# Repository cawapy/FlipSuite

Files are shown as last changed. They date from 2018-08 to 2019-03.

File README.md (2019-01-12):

# FlipSuite

KiCad schematics and PCBs for building flip dot and flip segment display drivers.

## USE AT YOUR OWN RISK

The designs are not yet finalized or not fully tested.

## Status

### Flips5, Flips6, Flips7

PCBs of [Flips5](Flips5), [Flips6](Flips6) and [Flips7](Flips7),
each in Version V1.0, have been manufactured and equiped.

Flips5, Flips6 and Flips7 can be considered working, at least in single display configurations. Successfully tested:

* Flips5 with standard Brose displays on ``BROSE60`` and ``BRDIC1``, connected to Flips6 on ``CNY1``+``CNY2`` and ``CNX1``
    * 28x16 (15 mm dots)
    * 28x19 (10 mm dots)
* Flips5 with extended 28x24 (10 mm dots) Brose display on ``BROSE60``+``BROSE20`` and ``BRDIC1``, connected to Flips6 on ``CNY1``+``CNY2`` and ``CNX1``
    * This display uses the 24 rows 3-26
* Flips5 with Brose display of 5 digits a 5x7 = 25x7 on ``BROSE34`` and ``BRDIC1``, connected to Flips6 on ``CNY1`` and``CNX1``
* Flips7 with Transit Media displays, connected to Flips6 ``CNY1``+``CNY2`` and ``CNX1``
    * 28x13 (15 mm dots)
    * 28x16 (15 mm dots)
    * 14x16 (15 mm dots)
    * 28x16 (10 mm dots)

Tests of multi display configurations with Flips6 are still pending.

### Flips8

[Flips8](Flips8) is work-in-progress.

## PCBs

View PCBs [online](PCBs.md).

## Known Issues V1.0

### Flips5

* ``R1``, ``R2``, ``R3`` and ``C1``, ``C2``, ``C3`` are too close to the DIP40 sockets of ``IC1``, ``IC2``, ``IC3``;
  When using standard DIP40 sockets with rectangular spring contacts,
  the socket frame and a pad of each of the mentioned resistors and capacitors will overlap.
    * Already rearranged the resistors and capacitors in the layout ([db15812: "Place FP2800As' bypass capacitors and EN-pulldowns to fit in Dip40 socket"](https://github.com/cawapy/FlipSuite/commit/db15812063dd6a5a91f173546fd940a55fbdb63b))
    * Options for manufactured boards
        * Use sockets with slimmer frame (e.g. those with round pins); or pin rows, they are also slimmer than the standard socket frames
        * Use little solder for Rs and Cs, decenter Rs and Cs away from socket frame as much as possible
        * Mill small holes into socket to not collide with housings of Rs and Cs
        * Do not equip the Flips5 PCB with those Rs and Cs
            * The enable signals should have pull down resistors, but they can be provided externally; the Flips6 already provides the enable signals *with* pull down resistors
            * The bypass capacitor can be omitted while the circuit will still work (but it *might* create more radio interferences then)
* Cannot use connector socket *with locks* for ``CN3`` due to conflict with ``BRDIC1`` connector

### Flips6

* Legend with pinout table of ``CN1`` has labels for pins 6 and 8 (``CLK`` vs. ``LAT``) swapped
    * Solution: in the layout, already fixed the table ([aecff96: "Fix wrong labels of Flips6 uP connector: LAT \<--\> CLK"](https://github.com/cawapy/FlipSuite/commit/aecff968aa479d9d29c823dc3a2e2e32617ff91e))

### Flips7

* The jumper ``JP1`` allowing to switch between 28 and 14 column display panel is not required.
  It turned out that both display types do *not* differ regarding pins of columns 4 (and 27).
  The 14 column panel can be used like the 28 column panel.
    * The jumper can be set or even soldered for the 28 column configuration.
    * Jumper to be removed in next version.

## Description

Here is some [technical description](Description.md).

## Flips Systems

* Brose
    * Matrix
        * Minimal:    [..-14 Rows (60P-Connector)](documentation/flips5-13rows.pdf)
        * Typical:    [15-20 Rows (60P-Connector; +**CNY2**)](documentation/flips5-19rows.pdf)
        * Extra:      [21-28 Rows (60P+**20P**-Connectors; +**CNY2**)](documentation/flips5-22rows.pdf)
        * Multi:      [Multiple Display Panels (+**CNX2**, ...)](documentation/flips5-19rows-x3.pdf)
    * Characters
        * [5 Positions a 5x7 Dots (34P-Connector)](documentation/flips5-07rows.pdf)
* Transit Media
    * Small:   [Display with ..-14 Rows](documentation/flips6-1flips7-minimal.pdf)
    * Typical: [Display with 14-16 Rows](documentation/flips6-1flips7.pdf)
    * Multi:   [Multiple Display Panels](documentation/flips6-3flips7.pdf)

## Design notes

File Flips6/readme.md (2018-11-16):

# Flips6

* View online with [cho45.stfuawsc.com KiCad viewer](https://cho45.stfuawsc.com/kicad-utils/static/viewer.html):
    * [PCB](https://cho45.stfuawsc.com/kicad-utils/static/viewer.html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)
    * [Schematics](https://cho45.stfuawsc.com/kicad-utils/static/viewer.html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)

* 2 independent groups of dependent ports for rows vs. columns
* controlled by 2-3 cascaded 595 shift registers

### Mapping

| # | R0 | R1 | R2?  |
|---|---|---|---|
| 0 | YA.0 | XA.0 | XEN3 |
| 1 | YA.1 | XA.1 | XEN4 |
| 2 | YA.2 | XA.2 | XEN5 |
| 3 | YB.0 | XB.0 | n.c. |
| 4 | YB.1 | XB.1 | n.c. |
| 5 | YDAT | XDAT | n.c. |
| 6 | YEN1 | XEN1 | n.c. |
| 7 | YEN2 | XEN2 | n.c. |

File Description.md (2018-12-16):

# FP2800A Based Drivers

[Flips5](Flips5) and [Flips7](Flips7) are driver boards for FlipDot display panels,
based on the FP2800A decoder/driver.
The major difference between Flips5 and Flips7 are the connector types and so the supported display panel types.

## Flips5

Flips5 is designed for
* Brose 60 Pin connector, widely used in flip dot matrix displays with 28 x 13..24 dots
    * Including the Brose 20 Pin extension connector for n > 20 rows
* Brose 34 Pin connector, such as 5 digits 5x7 flip dot display

### Row Pins of Brose 60 Pin Connector

| |1/2 |3/4 |5/6 |7/8 |9/10|11/12|13/14|15/16|17/18|19/20|21/22|23/24|25/26|27/28|29/30|31/32|33/34|35/36|37/38|39/40|41/42|43/44|45/46|47/48|49/50|51/52|53/54|55/56|57/58|59/60|
|-|----|----|----|----|----|-----|-----|-----|-----|-----|-----|-----|-----|-----|-----|-----|-----|-----|-----|-----|-----|-----|-----|-----|-----|-----|-----|-----|-----|-----|
|2|SY02|SY04|SY06|SY08|SY10|SY12 |SY14 |SY16 |SY18 |SY20 |/RY02|/RY04|/RY06|/RY08|/RY10|/RY12|/RY14|/RY16|/RY18|/RY20| | | | | | | | | | |
|1|SY01|SY03|SY05|SY07|SY09|SY11 |SY13 |SY15 |SY17 |SY19 |/RY01|/RY03|/RY05|/RY07|/RY09|/RY11|/RY13|/RY15|/RY17|/RY19| | | | | | | | | | |

* SY*nn* - Set dot in row *nn* by driving high (column to be driven low)
* /RY*nn* - Reset dot in row *nn* by driving low (column to be driven high)

### Row Pins of Brose 20 Pin Extension Connector

| |1/2 |3/4 |5/6 |7/8 |9/10 |11/12|13/14|15/16|17/18|19/20|
|-|----|----|----|----|-----|-----|-----|-----|-----|-----|
|2|SY22|SY24|SY26|SY28|/RY22|/RY24|/RY26|/RY28| | |
|1|SY21|SY23|SY25|SY27|/RY21|/RY23|/RY25|/RY27| | |

* SY*nn* - Set dot in row *nn* by driving high (column to be driven low)
* /RY*nn* - Reset dot in row *nn* by driving low (column to be driven high)

I have not seen a display with such connector, the above pin mapping has been reported to me.

### Row Pins of Brose 34 Pin Extension Connector

| |1/2 |3/4 |5/6 |7/8 |9/10|11/12|13/14|15/16|17/18|19/20|21/22|23/24|25/26|27/28|29/30|31/32|33/34|
|-|----|----|----|----|----|-----|-----|-----|-----|-----|-----|-----|-----|-----|-----|-----|-----|
|2| | | | | | | | | |/RY01|/RY02|/RY03|/RY04|/RY05|/RY06|/RY07| |
|1| | | | | | | | | |SY01 |SY02 |SY03 |SY04 |SY05 |SY06 |SY07 | |

* SY*nn* - Set dot in row *nn* by driving high (column to be driven low)
* /RY*nn* - Reset dot in row *nn* by driving low (column to be driven high)

## Flips7

Flips7 is designed for the Transit Media 60 Pin connector, used in different Transit Media flip dot matrix panels,
such as 28x13, 28x16 and 14x16 of different dot sizes.

### Transit Media Connector

|  |1/31 |2/32 |3/33|4/34|5/35 |6/36|7/37|8/38 |9/39|10/40|11/41|12/42|13/43|14/44|15/45|16/46|17/47|18/48|19/49|20/50|21/51|22/52|23/53|24/54|25/55|26/56|27/57|28/58|29/59|30/60|
|--|-----|-----|----|----|-----|----|----|-----|----|-----|-----|-----|-----|-----|-----|-----|-----|-----|-----|-----|-----|-----|-----|-----|-----|-----|-----|-----|-----|-----|
|31|/SY12|RY12 |X03 |X02 |X01  |X09 |RY13|/SY13|X08 |X07  |X06  |X05  |/SY10|X04\*|RY10 |X25  |X24  |X23  |/SY16|X22  |RY16 |RY15 |/SY15|X28  |X27\*|X26  |X21  |RY11 |X20  |/SY11|
| 1|X11  |/SY07|RY07|X12 |/SY06|RY06|X13 |/SY03|RY03|X14  |/SY02|X10  |RY02 |RY14 |/SY14|X15  |/SY01|RY01 |X16  |/SY04|RY04 |X17  |/SY05|RY05 |X18  |/SY08|RY08 |X19  |/SY09|RY09 |

* /SY*nn* - Set dot in row *nn* by driving low (column to be driven high)
* RY*nn* - Reset dot in row *nn* by driving high (column to be driven low)
* X*mm* - Set(Reset) dot in column *mm* by driving high(low)
* \*) On 14 column board, X04 is on position 55

Each Flips5/7 board is intended to drive **one** flip dot display panel.
It has a slot for **one** FP2800A, acting as the column driver for that panel.
The corresponding display panel boards support up to 28 columns,
but some are found with 16 or 25 (5 digits of 5 columns).
The 28 addressable outputs of the column driver FP2800A correspond to the 28 columns of the display panel.
The output-column assignment is linear;
(B1, B0, A2, A1, A0) = (0, 0, 0, 0, 1) corresponds to column 1,
while (B1, B0, A2, A1, A0) = (1, 1, 1, 1, 1) corresponds to column 28.
The Transit Media interface includes the column driver lines.
The Brose 60 Pin interface does not; instead, the column driver is located directly on the display panel board,
and only its control lines are included in the 60 Pin connector.
Unfortunately, often 24V are used as logic level, which cannot be easily provided by a micro controller.
For this reason, the column driver FP2800A is supposed to be put into Flips5, and the column driver lines
are injected via DIP40 adapter, fed from Flips5.
This allows to control the column driver by its native control lines using 5V logic.

Furthermore, each Flips5 and Flips7 board has **two** slots for **0 up to 2** FP2800As, acting as row driver(s).
Row driver outputs for the high and low side need to be separated;
for driving a single row, a source and another sink driver is required, which cannot be connected.
So while the FP2800A has 28 source and 28 sink drivers, only half of them can be used as row driver,
as they all are pairwise connected.
However, for scalability and saving FP2800As, the two FP2800As have not been split into 28 high and 28 low side drivers,
but into 14 high + 14 low side drivers for rows 1-14 and for rows 15-28.
When using up to 14 rows, a single FP2800A is sufficient.
When using 15-28 rows, two FP2800A are required.

In a multi panel setup, multiple display panels can share their row driver(s);
then each panel still requires its own Flips5/7 with the column driver for that panel,
but only a single of the Flips5/7 needs to be equiped with a set of row drivers.
The row driver lines of all display panels need to be connected then.
Boards with the Brose 60 pin connector typically have two such connectors,
so one of them can be used to feed the row driver lines from the Flips5 or the preceding display panel,
and the other one can be used to feed the succeeding display panels row drivers.
In contrast, the transit media displays lack of such multiple connectors, so each Flips7 has two
more connectors for sharing the row driver lines with previous and next.

So each Flips5 and Flips7 can contain 0-2 row driver FP2800As, depending on the number of rows and sharing or not sharing
the row driver(s) between display panels, and 1 column driver FP2800A.

All FP2800As on the Flip5 and Flips7 are controlled directly using the FP2800A interface consisting of
A[2..0], B[1..0], DATA and ENABLE.
For flexibility and scalability reasons, there is one 10 pin connector for each FP2800A, including the mentioned
7 control lines and supply such as VCC, VS and GND.
All those connectors have the same pin assignment.

## Controlling the FP2800A

Given there is a set of Flips5 or Flips7 for driving a set of display panels,
there is need to control each column driver and the shared row driver ICs.

Flips6 uses some 74595 shift registers to allow control words to be sent serially from the micro controller,
controlling the connected row and column drivers.

In FP2800A based displays with shared row drivers, only one dot can be driven at a time,
by activating that dots column driver in parallel to that dots row driver.
This means that even in a multi panel setup, there is always just one column activated, and one row.
This allows for sharing the control lines between all column drivers, and again sharing the control
lines between all row drivers.
Each except their ENABLE pins, which must be controlled individually.

Flips6 has 2 of the 10 Pin control connectors for row drivers, sharing all but ENABLE,
and 6 of that same connectors for column drivers, also sharing all but their ENABLE.
All ENABLE pins can be controlled individually.

This way, Flips6 allows for driving a matrix of width = 6 * 28 = 168, and height = 28 dots.

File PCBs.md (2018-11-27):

* View PCBs with [cho45.stfuawsc.com KiCad viewer](https://cho45.stfuawsc.com/kicad-utils/static/viewer.html):
    * [Flips5](https://cho45.stfuawsc.com/kicad-utils/static/viewer.html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)
    * [Flips6](https://cho45.stfuawsc.com/kicad-utils/static/viewer.html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)
    * [Flips7](https://cho45.stfuawsc.com/kicad-utils/static/viewer.html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)
    * [Flips8](https://cho45.stfuawsc.com/kicad-utils/static/viewer.html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)
    * [All](https://cho45.stfuawsc.com/kicad-utils/static/viewer.html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)

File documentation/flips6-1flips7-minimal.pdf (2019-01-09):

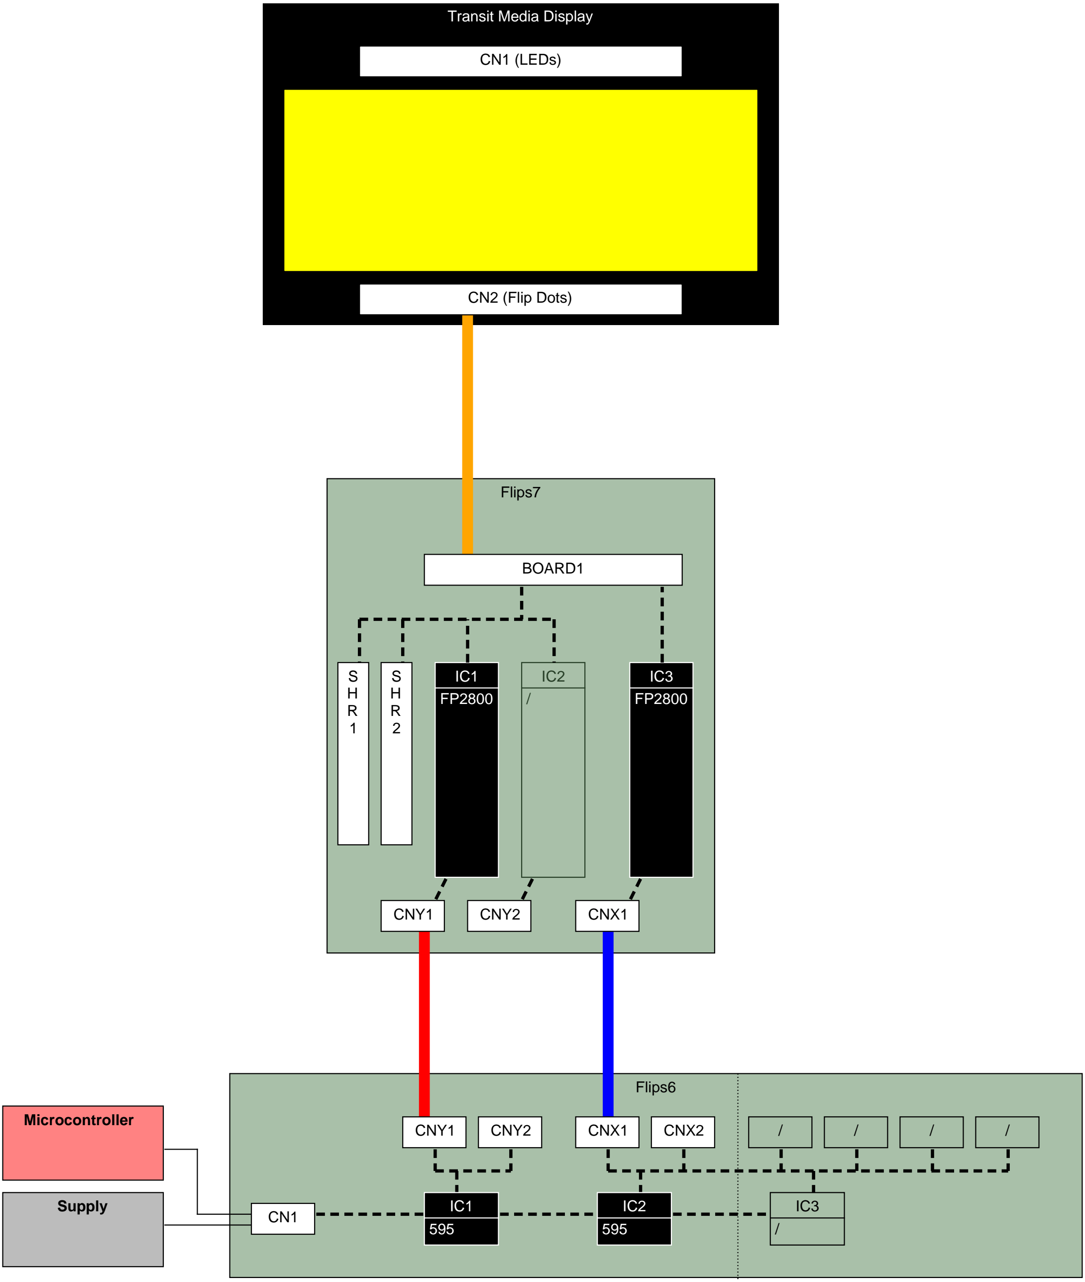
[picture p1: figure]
Supply; Transit Media Display; Microcontroller; Flips6; Flips7; CN1 (LEDs); CN2 (Flip Dots); CNY1; CNY2; CNX1; CNX2; BOARD1

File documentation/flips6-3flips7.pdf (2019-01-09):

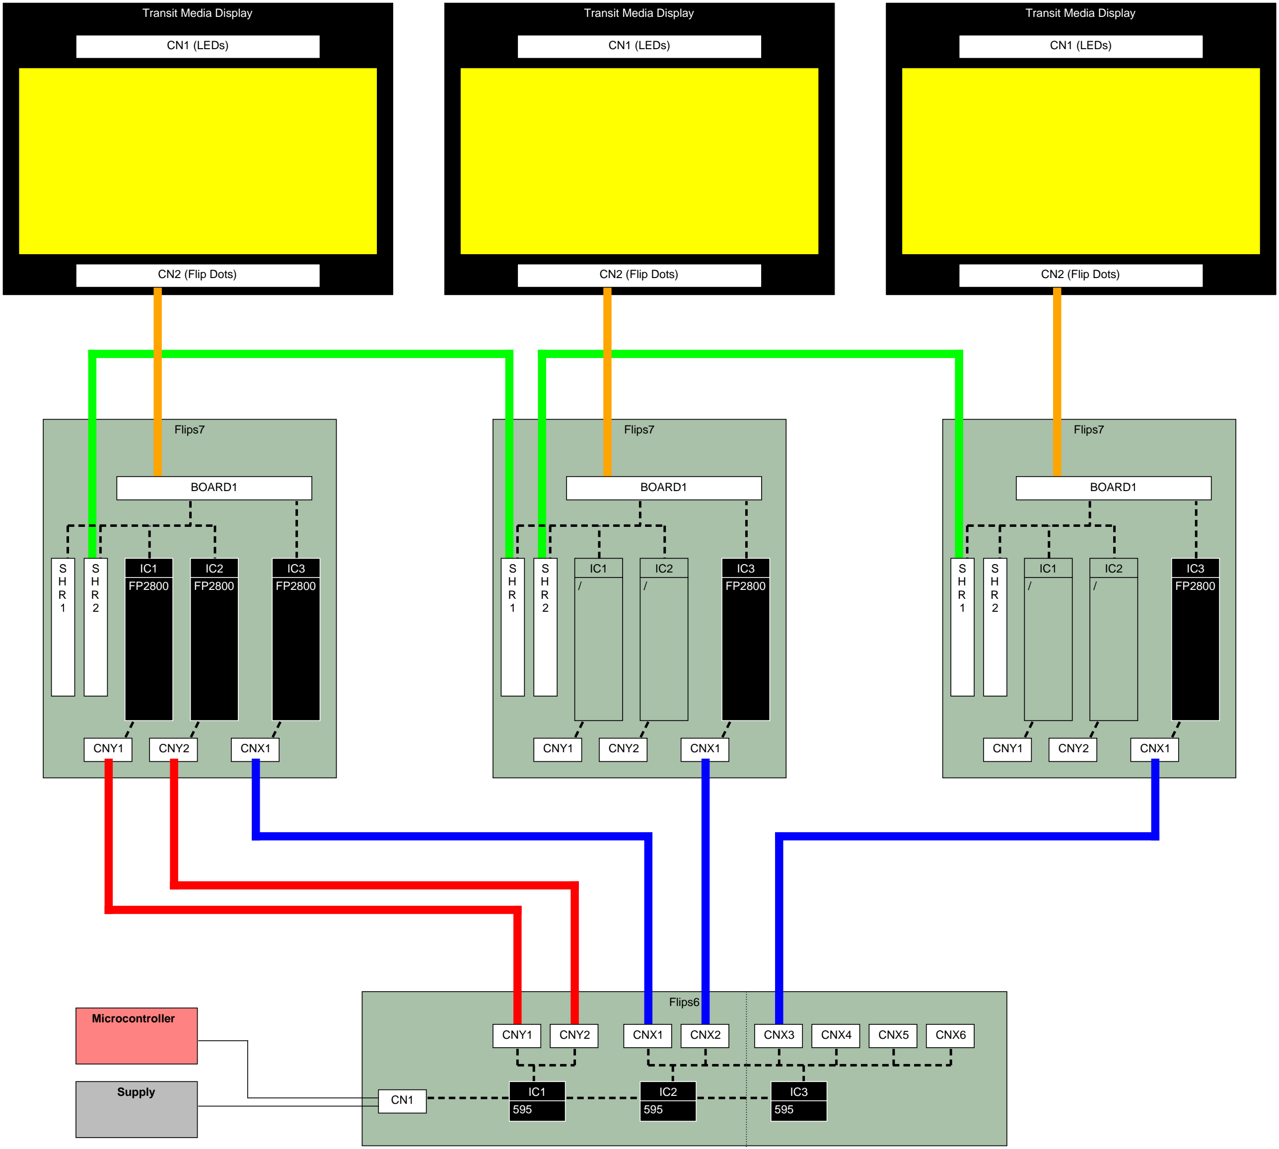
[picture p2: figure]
Transit Media Display; Flips7; Supply; Microcontroller; Flips6; CN1 (LEDs); CN2 (Flip Dots); BOARD1; CNY1; CNY2; CNX1; CNX2; CNX3; CNX4; CNX5; CNX6

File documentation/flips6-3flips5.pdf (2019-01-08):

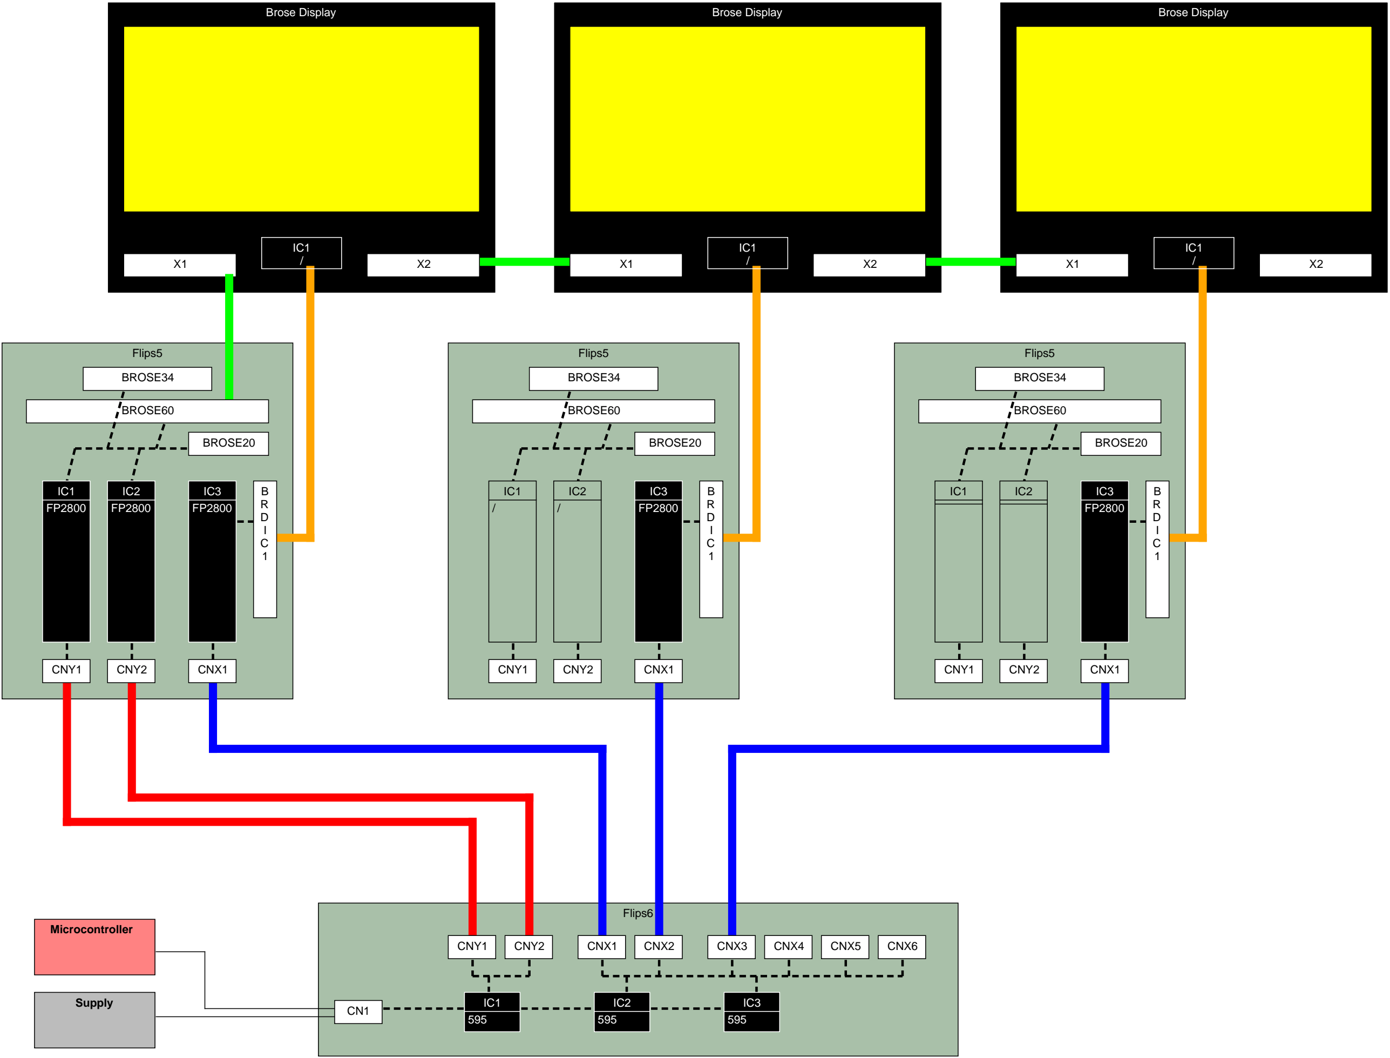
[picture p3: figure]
Supply; Brose Display; Microcontroller; Flips6; Flips5; CNY1; CNY2; CNX1; CNX2; CNX3; CNX4; CNX5; CNX6; BROSE34; BROSE20; BROSE60

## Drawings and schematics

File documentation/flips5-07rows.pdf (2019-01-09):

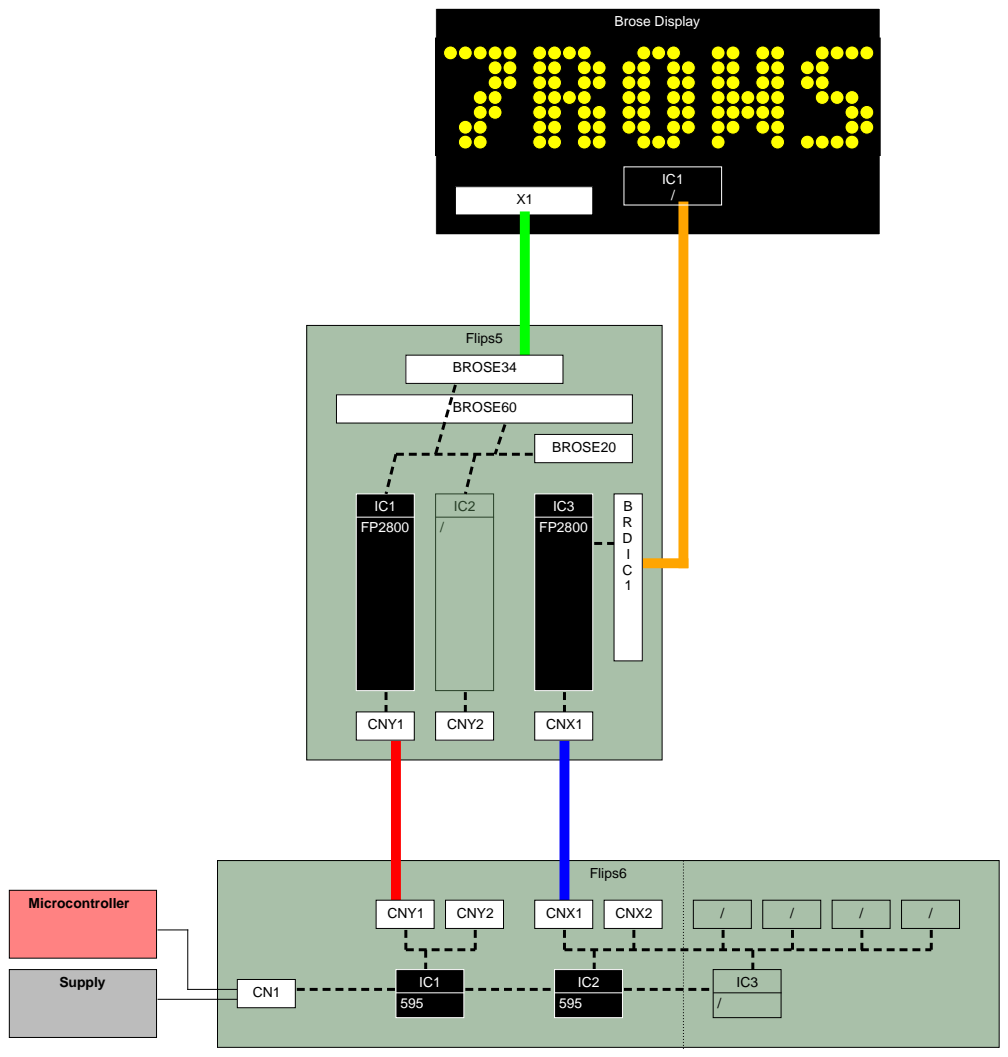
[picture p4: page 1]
Supply; Brose Display; Microcontroller; Flips6; Flips5; CNY1; CNY2; CNX1; CNX2; BROSE34; BROSE20; BROSE60

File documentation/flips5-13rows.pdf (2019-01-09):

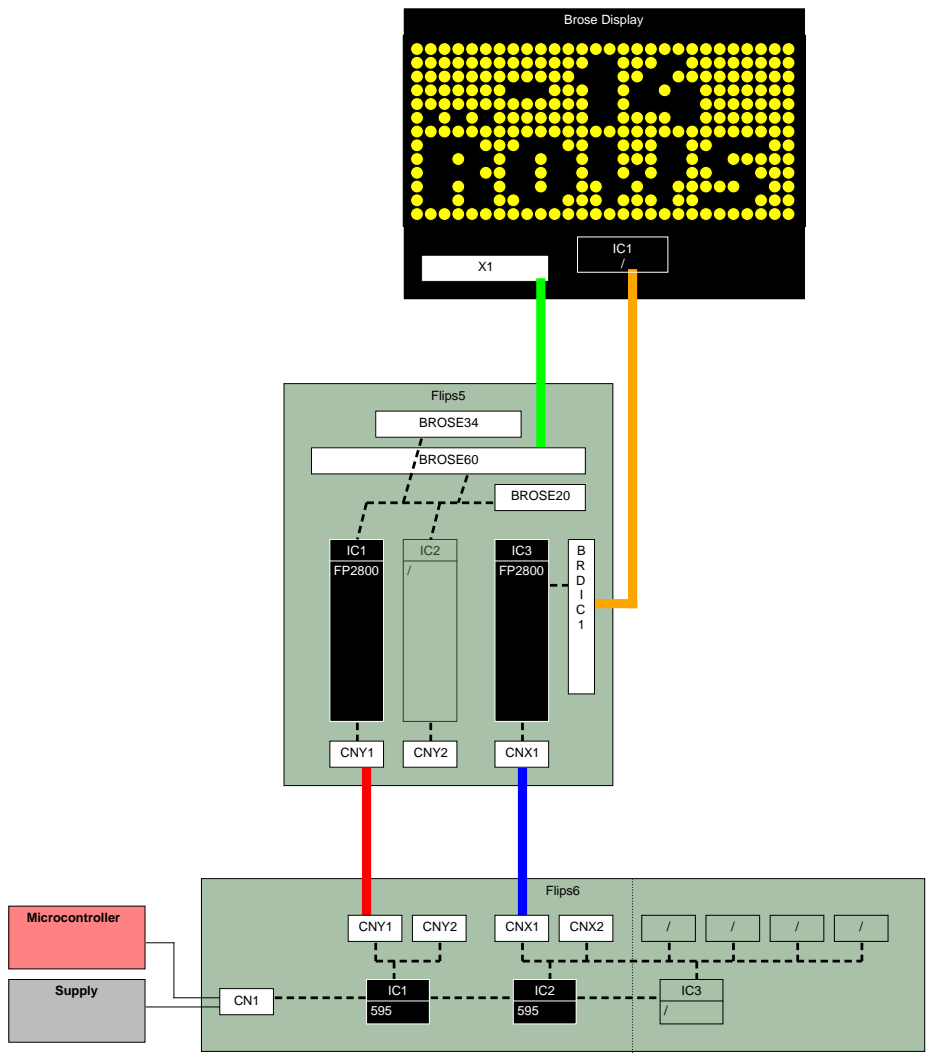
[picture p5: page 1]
Supply; Brose Display; Microcontroller; Flips6; Flips5; CNY1; CNY2; CNX1; CNX2; BROSE34; BROSE20; BROSE60

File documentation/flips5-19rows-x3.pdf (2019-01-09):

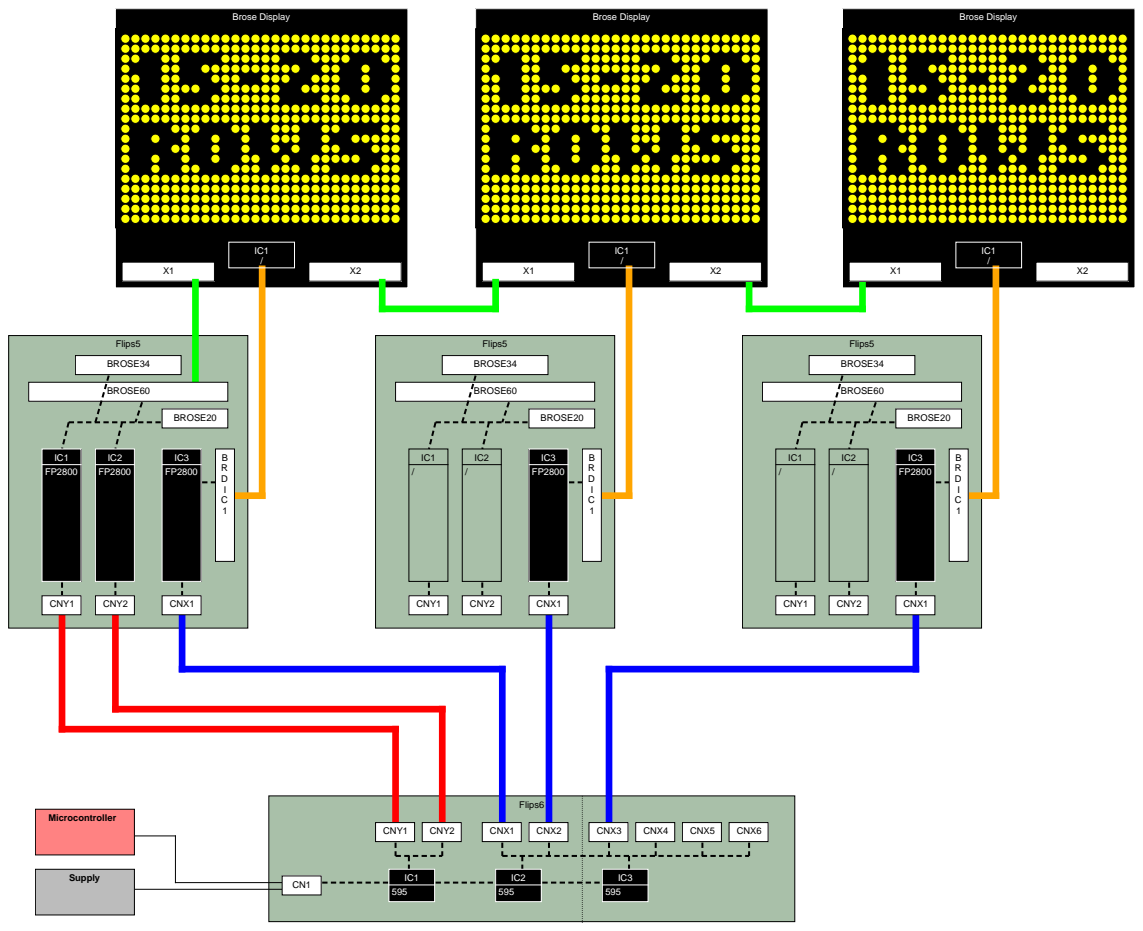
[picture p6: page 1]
Brose Display; Supply; Microcontroller; Flips6; Flips5; CNY1; CNY2; CNX1; CNX2; CNX3; CNX4; CNX5; CNX6; BROSE34; BROSE20; BROSE60

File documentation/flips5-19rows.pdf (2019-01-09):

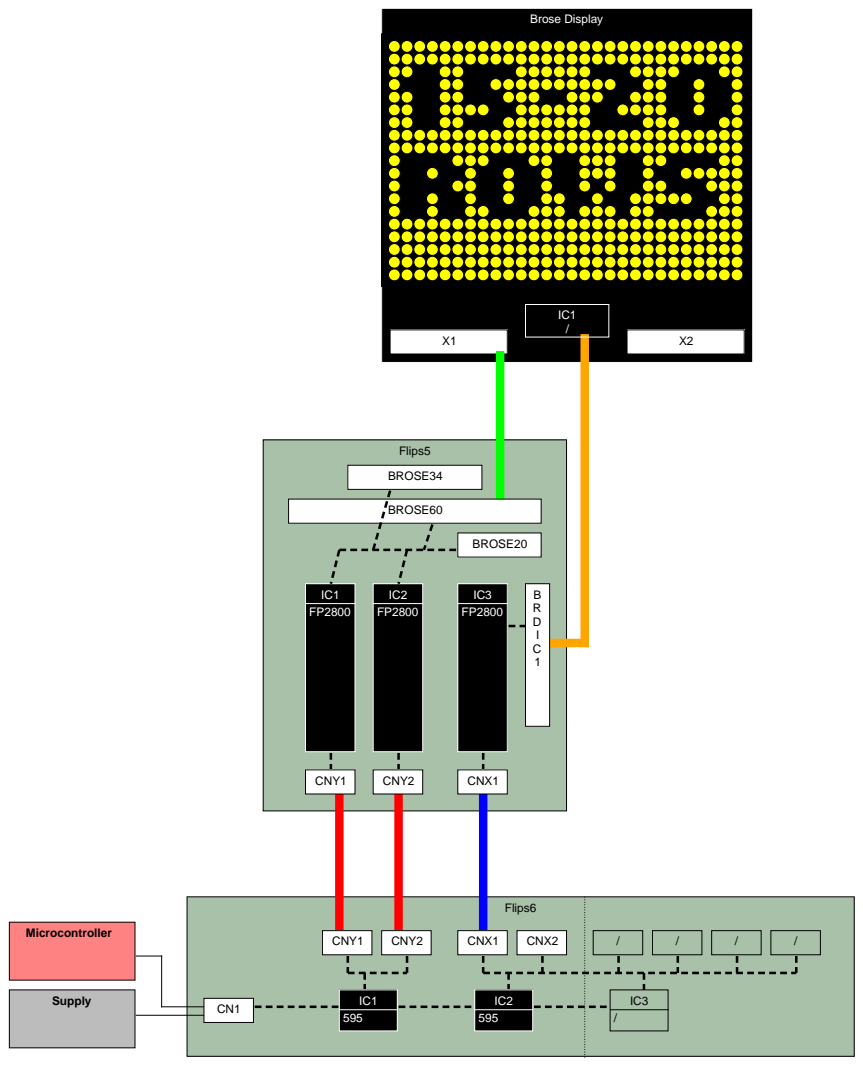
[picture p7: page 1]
Brose Display; Supply; Microcontroller; Flips6; Flips5; CNY1; CNY2; CNX1; CNX2; BROSE34; BROSE20; BROSE60

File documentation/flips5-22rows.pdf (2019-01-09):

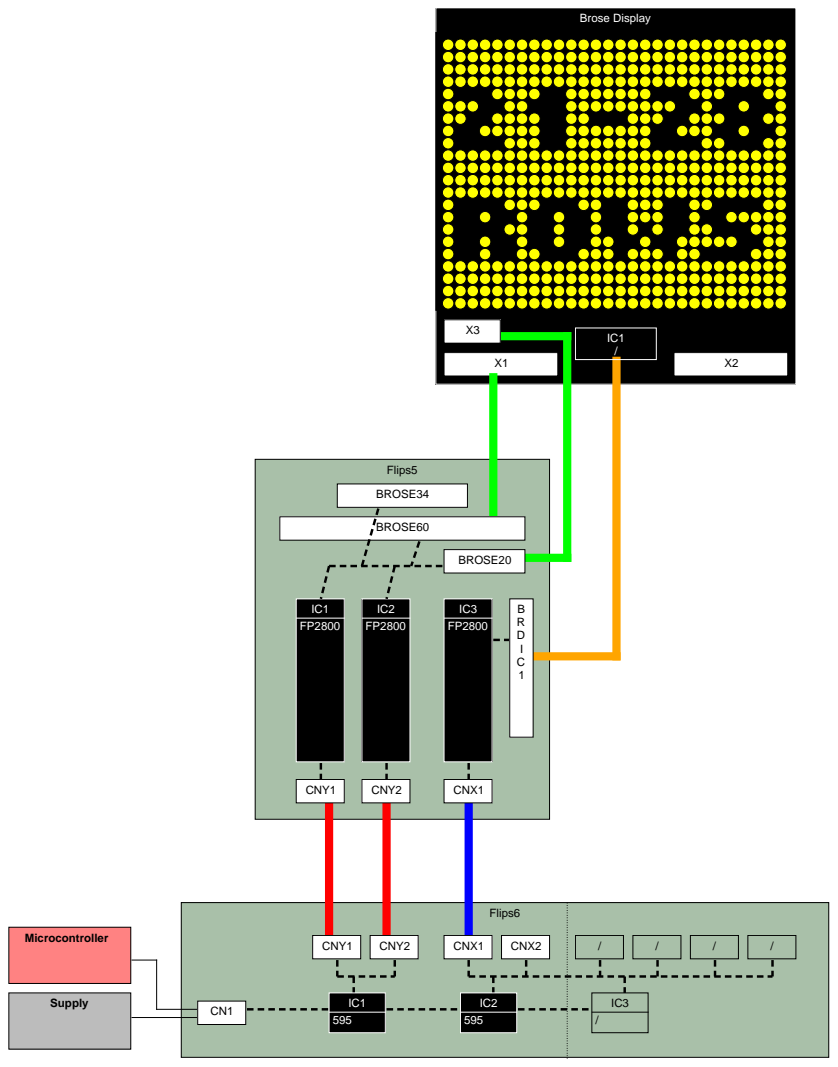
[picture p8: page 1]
Brose Display; Supply; Microcontroller; Flips6; Flips5; CNY1; CNY2; CNX1; CNX2; BROSE34; BROSE20; BROSE60

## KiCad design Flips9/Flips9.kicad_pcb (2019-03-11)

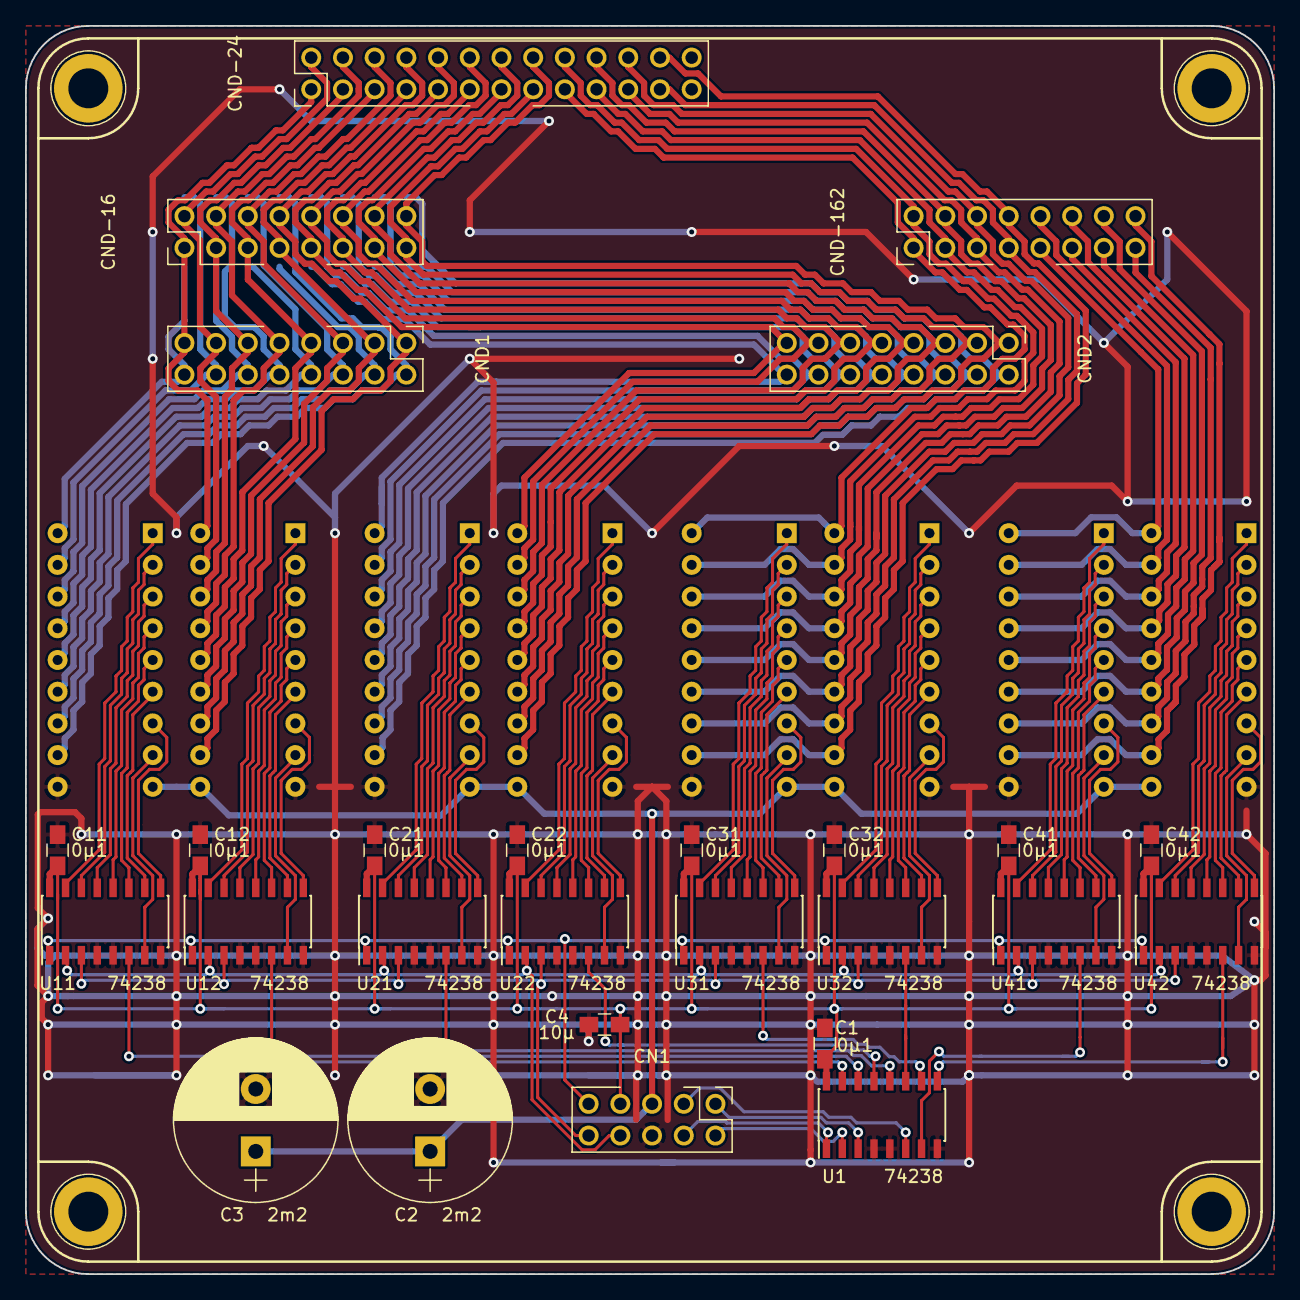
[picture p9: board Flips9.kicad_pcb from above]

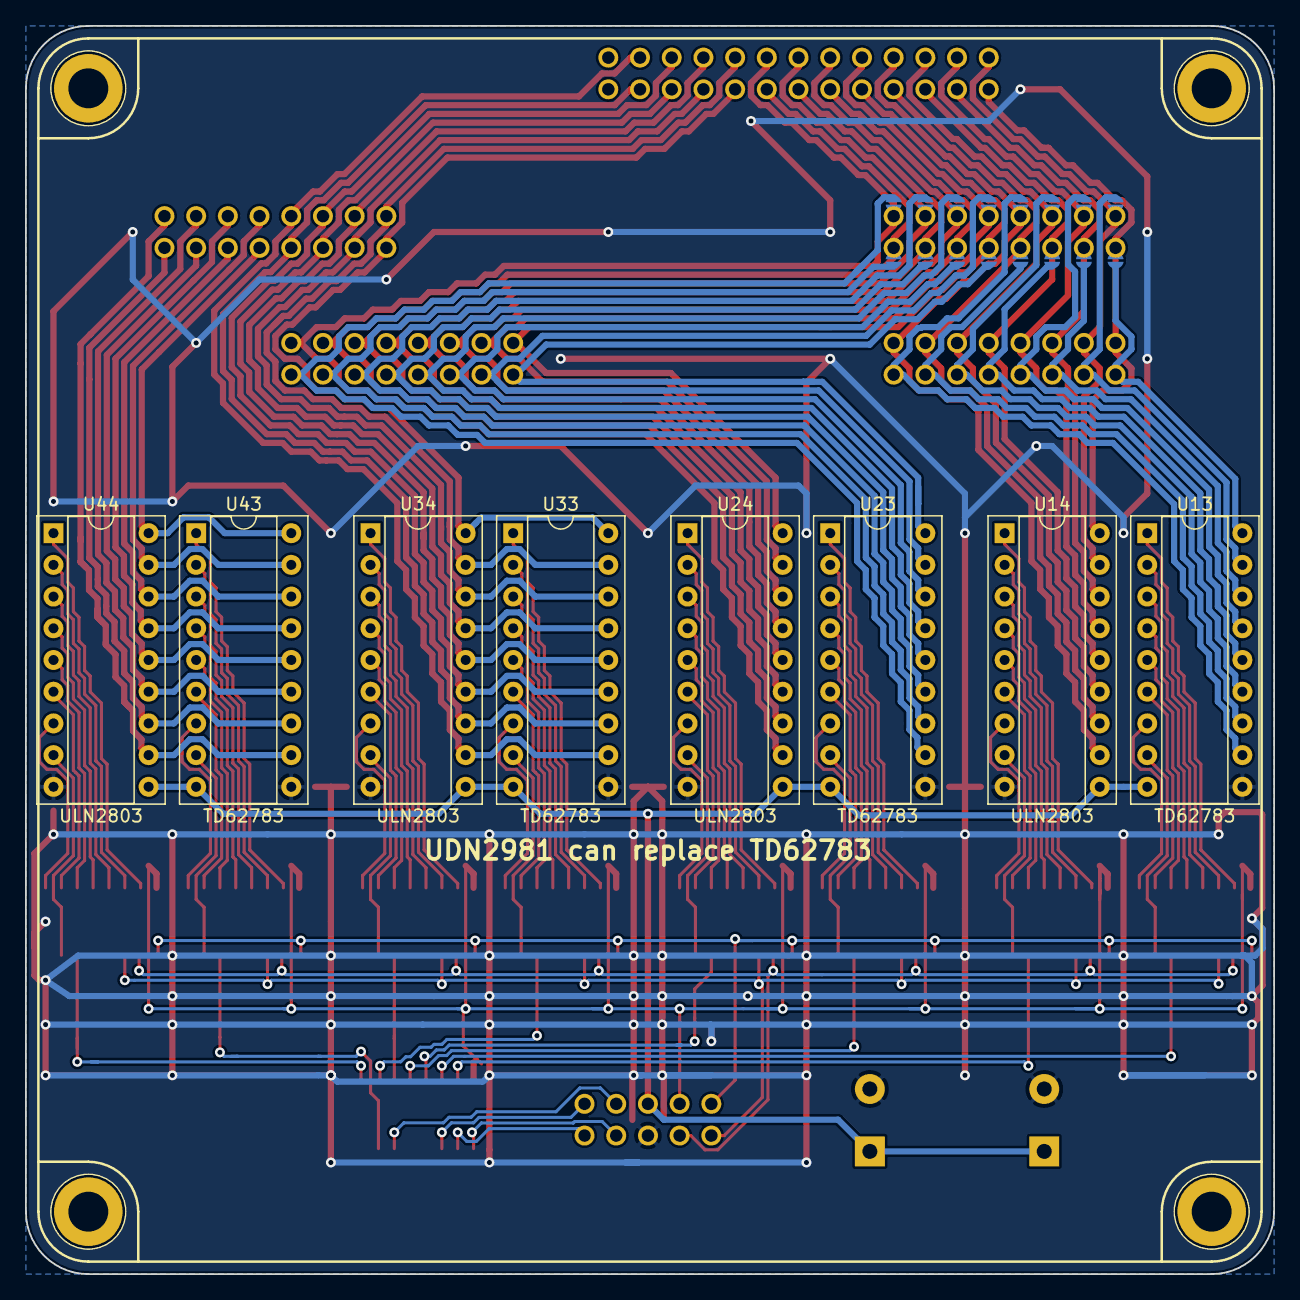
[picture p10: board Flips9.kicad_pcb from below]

Board: 2 copper layers, 100.0 x 100.0 mm, 55 parts (24 on the bottom side), 130 nets.

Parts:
C1, C11, C12, C21, C22, C31, C32, C41, C42: 0μ1; C_0805_HandSoldering
C2, C3: 2m2; CP_Radial_D13.0mm_P5.00mm
C4: 10µ; C_0805_HandSoldering
CN1: UFP2810; Pin_Header_Angle_Shrouded_2x05_Pitch2.54mm_ConvNumbering
CND1, CND2: Conn_02x08_Odd_Even; Pin_Header_Straight_Shrouded_Locks_2x08_Pitch2.54mm_ConvNum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
CND-16, CND-162: Conn_02x08_Odd_Even; Pin_Header_Straight_Shrouded_Locks_2x08_Pitch2.54mm_ConvNum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
CND-24: Conn_02x13_Odd_Even; Pin_Header_Straight_Shrouded_Locks_2x13_Pitch2.54mm_ConvNum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
H101, H102, H103, H104: MountingHole; MountingHole_3.2mm_M3_ISO14580_Pad
JP101, JP102, JP103, JP104, JP105, JP106, JP107, JP108, JP109, JP110, JP111, JP112, JP113, JP114, JP115, JP116: Jumper_NO_Small; SolderJumper1.3mmNoSilk
U1, U11, U12, U21, U22, U31, U32, U41, U42: 74238; SOIC-16_3.9x9.9mm_Pitch1.27mm
U13, U23, U33, U43: TD62783; DIP-18_W7.62mm_Socket
U14, U24, U34, U44: ULN2803; DIP-18_W7.62mm_Socket

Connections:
+24V: C2.1, C3.1, CN1.5, U13.9, U14.10, U23.9, U24.10, U33.9, U34.10, U43.9, U44.10
/SX1: CND1.16, JP101.1, U13.18
/SX2: CND1.14, JP102.1, U13.17
/SX3: CND1.12, JP103.1, U13.16
/SX4: CND1.10, JP104.1, U13.15
/SX5: CND1.8, JP105.1, U13.14
/SX6: CND1.6, JP106.1, U13.13
/SX7: CND1.4, JP107.1, U13.12
/SX8: CND1.2, JP108.1, U13.11
/SX9: CND2.16, JP109.1, U23.18
/SX10: CND2.14, JP110.1, U23.17
/SX11: CND2.12, JP111.1, U23.16
/SX12: CND2.10, JP112.1, U23.15
/SX13: CND2.8, JP113.1, U23.14
/SX14: CND2.6, JP114.1, U23.13
/SX15: CND2.4, JP115.1, U23.12
/SX16: CND2.2, JP116.1, U23.11
/UnitY/A0: CN1.9, U11.1, U12.1, U21.1, U22.1, U31.1, U32.1, U41.1, U42.1
/UnitY/A1: CN1.8, U11.2, U12.2, U21.2, U22.2, U31.2, U32.2, U41.2, U42.2
/UnitY/A2: CN1.10, U11.3, U12.3, U21.3, U22.3, U31.3, U32.3, U41.3, U42.3
/UnitY/B0: CN1.2, U1.2
/UnitY/B1: CN1.1, U1.3
/UnitY/DATA: CN1.4, U1.1
/UnitY/E0H: U1.14, U11.6
/UnitY/E0L: U1.15, U12.6
/UnitY/E1H: U1.12, U21.6
/UnitY/E1L: U1.13, U22.6
/UnitY/E2H: U1.10, U31.6
/UnitY/E2L: U1.11, U32.6
/UnitY/E3H: U1.7, U41.6
/UnitY/E3L: U1.9, U42.6
/UnitY/EN: CN1.3, U1.6
/UnitY/Group0/YH1: U11.14, U13.2
/UnitY/Group0/YH2: U11.13, U13.3
/UnitY/Group0/YH3: U11.12, U13.4
/UnitY/Group0/YH4: U11.11, U13.5
/UnitY/Group0/YH5: U11.10, U13.6
/UnitY/Group0/YH6: U11.9, U13.7
/UnitY/Group0/YH7: U11.7, U13.8
/UnitY/Group0/YL1: U12.14, U14.2
/UnitY/Group0/YL2: U12.13, U14.3
/UnitY/Group0/YL3: U12.12, U14.4
/UnitY/Group0/YL4: U12.11, U14.5
/UnitY/Group0/YL5: U12.10, U14.6
/UnitY/Group0/YL6: U12.9, U14.7
/UnitY/Group0/YL7: U12.7, U14.8
/UnitY/Group1/YH1: U21.14, U23.2
/UnitY/Group1/YH2: U21.13, U23.3
/UnitY/Group1/YH3: U21.12, U23.4
/UnitY/Group1/YH4: U21.11, U23.5
/UnitY/Group1/YH5: U21.10, U23.6
/UnitY/Group1/YH6: U21.9, U23.7
/UnitY/Group1/YH7: U21.7, U23.8
/UnitY/Group1/YL1: U22.14, U24.2
/UnitY/Group1/YL2: U22.13, U24.3
/UnitY/Group1/YL3: U22.12, U24.4
/UnitY/Group1/YL4: U22.11, U24.5
/UnitY/Group1/YL5: U22.10, U24.6
/UnitY/Group1/YL6: U22.9, U24.7
/UnitY/Group1/YL7: U22.7, U24.8
/UnitY/Group2/YH1: U31.14, U33.2
/UnitY/Group2/YH2: U31.13, U33.3
/UnitY/Group2/YH3: U31.12, U33.4
/UnitY/Group2/YH4: U31.11, U33.5
/UnitY/Group2/YH5: U31.10, U33.6
/UnitY/Group2/YH6: U31.9, U33.7
/UnitY/Group2/YH7: U31.7, U33.8
/UnitY/Group2/YL1: U32.14, U34.2
/UnitY/Group2/YL2: U32.13, U34.3
/UnitY/Group2/YL3: U32.12, U34.4
/UnitY/Group2/YL4: U32.11, U34.5
/UnitY/Group2/YL5: U32.10, U34.6
/UnitY/Group2/YL6: U32.9, U34.7
/UnitY/Group2/YL7: U32.7, U34.8
/UnitY/Group3/YH1: U41.14, U43.2
/UnitY/Group3/YH2: U41.13, U43.3
/UnitY/Group3/YH3: U41.12, U43.4
/UnitY/Group3/YH4: U41.11, U43.5
/UnitY/Group3/YH5: U41.10, U43.6
/UnitY/Group3/YH6: U41.9, U43.7
/UnitY/Group3/YH7: U41.7, U43.8
/UnitY/Group3/YL1: U42.14, U44.2
/UnitY/Group3/YL2: U42.13, U44.3
/UnitY/Group3/YL3: U42.12, U44.4
/UnitY/Group3/YL4: U42.11, U44.5
/UnitY/Group3/YL5: U42.10, U44.6
/UnitY/Group3/YL6: U42.9, U44.7
/UnitY/Group3/YL7: U42.7, U44.8
/Y1: CND1.15, CND-16.1, CND-24.1, JP101.2, U14.18
/Y2: CND1.13, CND-16.2, CND-24.2, JP102.2, U14.17
/Y3: CND1.11, CND-16.3, CND-24.3, JP103.2, U14.16
/Y4: CND1.9, CND-16.4, CND-24.4, JP104.2, U14.15
/Y5: CND1.7, CND-16.5, CND-24.5, JP105.2, U14.14
/Y6: CND1.5, CND-16.6, CND-24.6, JP106.2, U14.13
/Y7: CND1.3, CND-16.7, CND-24.7, JP107.2, U14.12
/Y8: CND1.1, CND-16.8, CND-24.8, JP108.2, U14.11
/Y9: CND2.15, CND-16.9, CND-24.9, JP109.2, U24.18
/Y10: CND2.13, CND-16.10, CND-24.10, JP110.2, U24.17
/Y11: CND2.11, CND-16.11, CND-24.11, JP111.2, U24.16
/Y12: CND2.9, CND-16.12, CND-24.12, JP112.2, U24.15
/Y13: CND2.7, CND-16.13, CND-24.13, JP113.2, U24.14
/Y14: CND2.5, CND-16.14, CND-24.14, JP114.2, U24.13
/Y15: CND2.3, CND-16.15, CND-24.15, JP115.2, U24.12
/Y16: CND2.1, CND-16.16, CND-24.16, JP116.2, U24.11
/Y17: CND-24.17, CND-162.1, U33.18, U34.18
/Y18: CND-24.18, CND-162.2, U33.17, U34.17
/Y19: CND-24.19, CND-162.3, U33.16, U34.16
/Y20: CND-24.20, CND-162.4, U33.15, U34.15
/Y21: CND-24.21, CND-162.5, U33.14, U34.14
/Y22: CND-24.22, CND-162.6, U33.13, U34.13
/Y23: CND-24.23, CND-162.7, U33.12, U34.12
/Y24: CND-24.24, CND-162.8, U33.11, U34.11
/Y25: CND-162.9, U43.18, U44.18
/Y26: CND-162.10, U43.17, U44.17
/Y27: CND-162.11, U43.16, U44.16
/Y28: CND-162.12, U43.15, U44.15
/Y29: CND-162.13, U43.14, U44.14
/Y30: CND-162.14, U43.13, U44.13
/Y31: CND-162.15, U43.12, U44.12
/Y32: CND-162.16, U43.11, U44.11
GND: C1.2, C2.2, C3.2, C4.2, C11.2, C12.2, C21.2, C22.2, C31.2, C32.2, C41.2, C42.2, CN1.6, U1.4, U1.5, U1.8, U11.4, U11.5, U11.8, U12.4, U12.5, U12.8, U13.10, U14.9, U21.4, U21.5, U21.8, U22.4, U22.5, U22.8, U23.10, U24.9, U31.4, U31.5, U31.8, U32.4, U32.5, U32.8, U33.10, U34.9, U41.4, U41.5, U41.8, U42.4, U42.5, U42.8, U43.10, U44.9
unnamed: U11.15, U13.1
unnamed: U12.15, U14.1
unnamed: U21.15, U23.1
unnamed: U22.15, U24.1
unnamed: U31.15, U33.1
unnamed: U32.15, U34.1
unnamed: U41.15, U43.1
unnamed: U42.15, U44.1
VCC: C1.1, C4.1, C11.1, C12.1, C21.1, C22.1, C31.1, C32.1, C41.1, C42.1, CN1.7, U1.16, U11.16, U12.16, U21.16, U22.16, U31.16, U32.16, U41.16, U42.16

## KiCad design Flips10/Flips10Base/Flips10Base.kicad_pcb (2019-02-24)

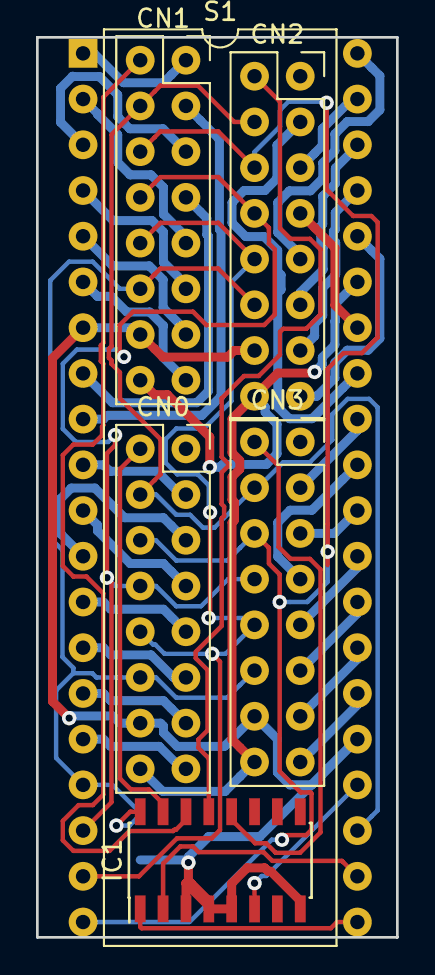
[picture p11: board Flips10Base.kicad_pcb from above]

Board: 2 copper layers, 20.0 x 50.0 mm, 7 parts (1 on the bottom side), 43 nets.

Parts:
C1: 0μ1; C_0805_HandSoldering
CN0, CN1, CN2, CN3: SR28GR; Socket_Strip_Straight_2x08_Pitch2.54mm
IC1: 74138; SOIC-16_3.9x9.9mm_Pitch1.27mm
S1: FP2800A-Interface; DIP-40_W15.24mm

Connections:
+24V: CN0.16, CN1.16, CN2.16, CN3.16, S1.35
/0A: CN0.15, S1.16
/0B: CN0.13, S1.15
/0C: CN0.11, S1.14
/0D: CN0.9, S1.13
/0E: CN0.7, S1.11
/0F: CN0.5, S1.12
/0G: CN0.3, S1.10
/1A: CN1.15, S1.6
/1B: CN1.13, S1.5
/1C: CN1.11, S1.4
/1D: CN1.9, S1.2
/1E: CN1.7, S1.8
/1F: CN1.5, S1.3
/1G: CN1.3, S1.9
/2A: CN2.15, S1.36
/2B: CN2.13, S1.37
/2C: CN2.11, S1.38
/2D: CN2.9, S1.40
/2E: CN2.7, S1.34
/2F: CN2.5, S1.39
/2G: CN2.3, S1.33
/3A: CN3.15, S1.26
/3B: CN3.13, S1.27
/3C: CN3.11, S1.28
/3D: CN3.9, S1.29
/3E: CN3.7, S1.31
/3F: CN3.5, S1.30
/3G: CN3.3, S1.32
/A0: CN0.10, CN1.10, CN2.10, CN3.10, S1.19
/A1: CN0.8, CN1.8, CN2.8, CN3.8, S1.18
/A2: CN0.6, CN1.6, CN2.6, CN3.6, S1.20
/B0: IC1.1, S1.21
/B1: IC1.2, S1.22
/COM: CN1.1, S1.1
/DATA: CN0.4, CN1.4, CN2.4, CN3.4, S1.23
/EN: IC1.6, S1.24
/~ENGR0: CN0.2, IC1.15
/~ENGR1: CN1.2, IC1.14
/~ENGR2: CN2.2, IC1.13
/~ENGR3: CN3.2, IC1.12
GND: C1.2, CN0.14, CN1.14, CN2.14, CN3.14, IC1.3, IC1.4, IC1.5, IC1.8, S1.7, S1.25
VCC: C1.1, CN0.12, CN1.12, CN2.12, CN3.12, IC1.16, S1.17

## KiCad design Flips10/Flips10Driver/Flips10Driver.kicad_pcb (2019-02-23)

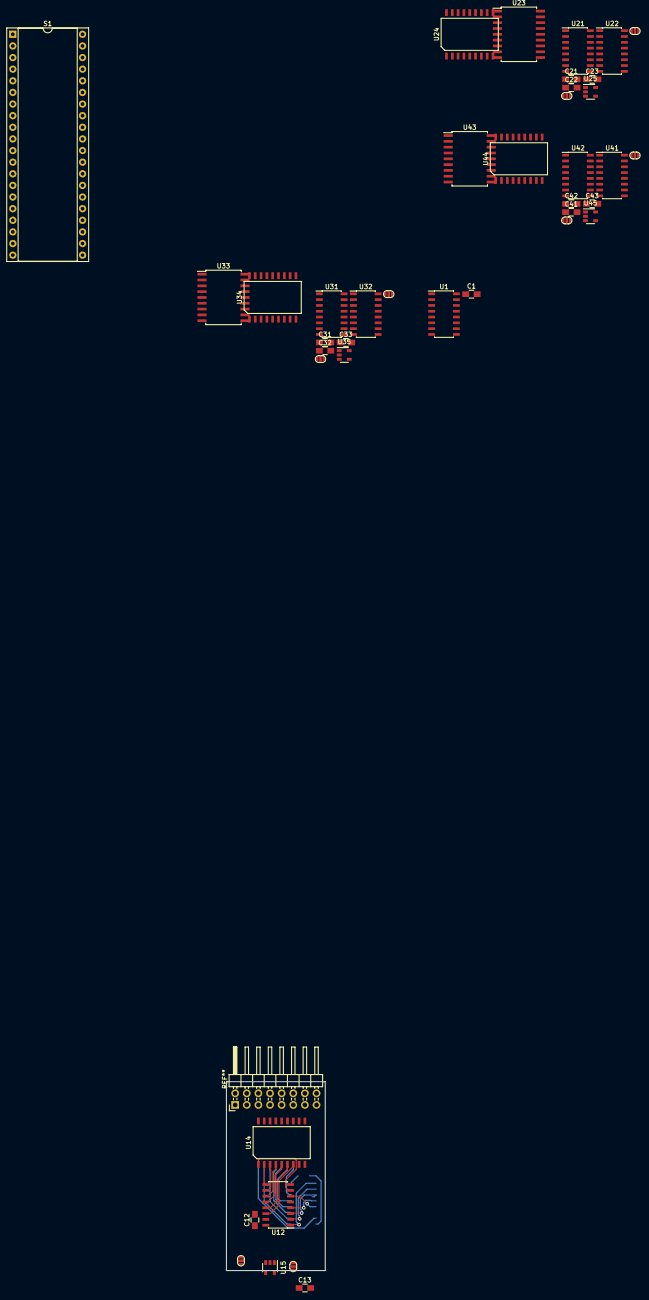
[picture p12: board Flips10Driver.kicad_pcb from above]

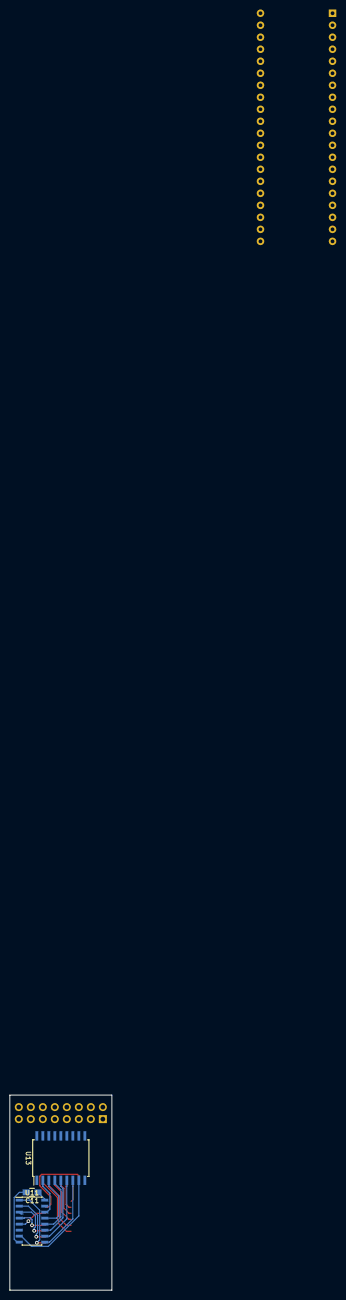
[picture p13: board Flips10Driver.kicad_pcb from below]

Board: 2 copper layers, 21.6 x 41.3 mm, 43 parts (3 on the bottom side), 114 nets.

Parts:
C1, C11, C12, C13, C21, C22, C23, C31, C32, C33, C41, C42, C43: 0μ1; C_0805_HandSoldering
JP11, JP12, JP21, JP22, JP31, JP32, JP41, JP42: Jumper; SolderJumper1.3mmChoice
S1: FP2800A; DIP-40_W15.24mm_Socket
U1: 74138; SOIC-16_3.9x9.9mm_Pitch1.27mm
U11, U12, U21, U22, U31, U32, U41, U42: 74238; SOIC-16_3.9x9.9mm_Pitch1.27mm
U13, U23, U33, U43: ULN2803/2003; SOIC-18W_7.5x11.6mm_Pitch1.27mm
U14, U24, U34, U44: TD62783; SOP18
U15, U25, U35, U45: 741G04; SOT-23-5

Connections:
+24V: S1.35, U13.10, U14.9, U23.10, U24.9, U33.10, U34.9, U43.10, U44.9
/0A: S1.16, U13.17, U14.12
/0B: S1.15, U13.16, U14.13
/0C: S1.14, U13.15, U14.14
/0D: S1.13, U13.14, U14.15
/0E: S1.11, U13.13, U14.16
/0F: S1.12, U13.12, U14.17
/0G: S1.10, U13.11, U14.18
/1A: S1.6, U23.17, U24.12
/1B: S1.5, U23.16, U24.13
/1C: S1.4, U23.15, U24.14
/1D: S1.2, U23.14, U24.15
/1E: S1.8, U23.13, U24.16
/1F: S1.3, U23.12, U24.17
/1G: S1.9, U23.11, U24.18
/2A: S1.36, U33.17, U34.12
/2B: S1.37, U33.16, U34.13
/2C: S1.38, U33.15, U34.14
/2D: S1.40, U33.14, U34.15
/2E: S1.34, U33.13, U34.16
/2F: S1.39, U33.12, U34.17
/2G: S1.33, U33.11, U34.18
/3A: S1.26, U43.17, U44.12
/3B: S1.27, U43.16, U44.13
/3C: S1.28, U43.15, U44.14
/3D: S1.29, U43.14, U44.15
/3E: S1.31, U43.13, U44.16
/3F: S1.30, U43.12, U44.17
/3G: S1.32, U43.11, U44.18
/A0: S1.19, U11.1, U12.1, U21.1, U22.1, U31.1, U32.1, U41.1, U42.1
/A1: S1.18, U11.2, U12.2, U21.2, U22.2, U31.2, U32.2, U41.2, U42.2
/A2: S1.20, U11.3, U12.3, U21.3, U22.3, U31.3, U32.3, U41.3, U42.3
/B0: S1.21, U1.1
/B1: S1.22, U1.2
/COM: S1.1, U13.18, U14.11
/DATA: JP11.3, JP21.3, JP31.3, JP41.3, S1.23, U11.5, U12.6, U15.2, U21.5, U22.6, U25.2, U31.5, U32.6, U35.2, U41.5, U42.6, U45.2
/EN: S1.24, U1.6
/UnitY/Group0/YH0: JP12.2, U14.8
/UnitY/Group0/YH1: U12.14, U14.7
/UnitY/Group0/YH2: U12.13, U14.6
/UnitY/Group0/YH3: U12.12, U14.5
/UnitY/Group0/YH4: U12.11, U14.4
/UnitY/Group0/YH5: U12.10, U14.3
/UnitY/Group0/YH6: U12.9, U14.2
/UnitY/Group0/YH7: U12.7, U14.1
/UnitY/Group0/YL0: JP11.2, U13.1
/UnitY/Group0/YL1: U11.14, U13.2
/UnitY/Group0/YL2: U11.13, U13.3
/UnitY/Group0/YL3: U11.12, U13.4
/UnitY/Group0/YL4: U11.11, U13.5
/UnitY/Group0/YL5: U11.10, U13.6
/UnitY/Group0/YL6: U11.9, U13.7
/UnitY/Group0/YL7: U11.7, U13.8
/UnitY/Group0/~DATA: JP12.3, U15.4
/UnitY/Group1/O0: U23.18, U24.11
/UnitY/Group1/YH0: JP22.2, U24.8
/UnitY/Group1/YH1: U22.14, U24.7
/UnitY/Group1/YH2: U22.13, U24.6
/UnitY/Group1/YH3: U22.12, U24.5
/UnitY/Group1/YH4: U22.11, U24.4
/UnitY/Group1/YH5: U22.10, U24.3
/UnitY/Group1/YH6: U22.9, U24.2
/UnitY/Group1/YH7: U22.7, U24.1
/UnitY/Group1/YL0: JP21.2, U23.1
/UnitY/Group1/YL1: U21.14, U23.2
/UnitY/Group1/YL2: U21.13, U23.3
/UnitY/Group1/YL3: U21.12, U23.4
/UnitY/Group1/YL4: U21.11, U23.5
/UnitY/Group1/YL5: U21.10, U23.6
/UnitY/Group1/YL6: U21.9, U23.7
/UnitY/Group1/YL7: U21.7, U23.8
/UnitY/Group1/~DATA: JP22.3, U25.4
/UnitY/Group2/O0: U33.18, U34.11
/UnitY/Group2/YH0: JP32.2, U34.8
/UnitY/Group2/YH1: U32.14, U34.7
/UnitY/Group2/YH2: U32.13, U34.6
/UnitY/Group2/YH3: U32.12, U34.5
/UnitY/Group2/YH4: U32.11, U34.4
/UnitY/Group2/YH5: U32.10, U34.3
/UnitY/Group2/YH6: U32.9, U34.2
/UnitY/Group2/YH7: U32.7, U34.1
/UnitY/Group2/YL0: JP31.2, U33.1
/UnitY/Group2/YL1: U31.14, U33.2
/UnitY/Group2/YL2: U31.13, U33.3
/UnitY/Group2/YL3: U31.12, U33.4
/UnitY/Group2/YL4: U31.11, U33.5
/UnitY/Group2/YL5: U31.10, U33.6
/UnitY/Group2/YL6: U31.9, U33.7
/UnitY/Group2/YL7: U31.7, U33.8
/UnitY/Group2/~DATA: JP32.3, U35.4
/UnitY/Group3/O0: U43.18, U44.11
/UnitY/Group3/YH0: JP42.2, U44.8
/UnitY/Group3/YH1: U42.14, U44.7
/UnitY/Group3/YH2: U42.13, U44.6
/UnitY/Group3/YH3: U42.12, U44.5
/UnitY/Group3/YH4: U42.11, U44.4
/UnitY/Group3/YH5: U42.10, U44.3
/UnitY/Group3/YH6: U42.9, U44.2
/UnitY/Group3/YH7: U42.7, U44.1
/UnitY/Group3/YL0: JP41.2, U43.1
/UnitY/Group3/YL1: U41.14, U43.2
/UnitY/Group3/YL2: U41.13, U43.3
/UnitY/Group3/YL3: U41.12, U43.4
/UnitY/Group3/YL4: U41.11, U43.5
/UnitY/Group3/YL5: U41.10, U43.6
/UnitY/Group3/YL6: U41.9, U43.7
/UnitY/Group3/YL7: U41.7, U43.8
/UnitY/Group3/~DATA: JP42.3, U45.4
/UnitY/~ENGR0: U1.15, U11.4, U12.4
/UnitY/~ENGR1: U1.14, U21.4, U22.4
/UnitY/~ENGR2: U1.13, U31.4, U32.4
/UnitY/~ENGR3: U1.12, U41.4, U42.4
GND: C1.2, C11.2, C12.2, C13.2, C21.2, C22.2, C23.2, C31.2, C32.2, C33.2, C41.2, C42.2, C43.2, JP11.1, JP12.1, JP21.1, JP22.1, JP31.1, JP32.1, JP41.1, JP42.1, S1.7, S1.25, U1.3, U1.4, U1.5, U1.8, U11.8, U12.5, U12.8, U13.9, U14.10, U15.3, U21.8, U22.5, U22.8, U23.9, U24.10, U25.3, U31.8, U32.5, U32.8, U33.9, U34.10, U35.3, U41.8, U42.5, U42.8, U43.9, U44.10, U45.3
VCC: C1.1, C11.1, C12.1, C13.1, C21.1, C22.1, C23.1, C31.1, C32.1, C33.1, C41.1, C42.1, C43.1, S1.17, U1.16, U11.6, U11.16, U12.16, U15.5, U21.6, U21.16, U22.16, U25.5, U31.6, U31.16, U32.16, U35.5, U41.6, U41.16, U42.16, U45.5

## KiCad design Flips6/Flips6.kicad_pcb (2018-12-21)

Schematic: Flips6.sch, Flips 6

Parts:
C1, C2, C3: 0µ1; C_0805_HandSoldering
CN1: Conn_02x04_Odd_Even; Pin_Header_Straight_2x04_Pitch2.54mm
CNX1, CNX2, CNX3, CNX4, CNX5, CNX6: UFP2810; Pin_Header_Straight_Shrouded_2x05_Pitch2.54mm
CNY1, CNY2: UFP2810; Pin_Header_Straight_Shrouded_2x05_Pitch2.54mm
IC1, IC2, IC3: 74595; SOIC-16_3.9x9.9mm_Pitch1.27mm
R1, R2, R3, R4, R5, R6, R7, R8, R9, R10: 10k; R_0805_HandSoldering

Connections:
+5V: C1.1, C2.1, C3.1, CN1.1, CNX1.7, CNX2.7, CNX3.7, CNX4.7, CNX5.7, CNX6.7, CNY1.7, CNY2.7, IC1.16 (VCC), IC2.16 (VCC), IC3.16 (VCC), R1.2, R2.2
+12V: CN1.3, CNX1.5, CNX2.5, CNX3.5, CNX4.5, CNX5.5, CNX6.5, CNY1.5, CNY2.5
/DIN: CN1.7, IC1.14 (SER)
/RCLK: CN1.8, IC1.12 (RCLK), IC2.12 (RCLK), IC3.12 (RCLK)
/SRCLK: CN1.6, IC1.11 (SRCLK), IC2.11 (SRCLK), IC3.11 (SRCLK)
/XA.0: CNX1.9, CNX2.9, CNX3.9, CNX4.9, CNX5.9, CNX6.9, IC2.15 (QA)
/XA.1: CNX1.8, CNX2.8, CNX3.8, CNX4.8, CNX5.8, CNX6.8, IC2.1 (QB)
/XA.2: CNX1.10, CNX2.10, CNX3.10, CNX4.10, CNX5.10, CNX6.10, IC2.2 (QC)
/XB.0: CNX1.2, CNX2.2, CNX3.2, CNX4.2, CNX5.2, CNX6.2, IC2.3 (QD)
/XB.1: CNX1.1, CNX2.1, CNX3.1, CNX4.1, CNX5.1, CNX6.1, IC2.4 (QE)
/XDAT: CNX1.4, CNX2.4, CNX3.4, CNX4.4, CNX5.4, CNX6.4, IC2.5 (QF)
/XEN1: CNX1.3, IC2.6 (QG), R5.2
/XEN2: CNX2.3, IC2.7 (QH), R6.2
/XEN3: CNX3.3, IC3.15 (QA), R7.2
/XEN4: CNX4.3, IC3.1 (QB), R8.2
/XEN5: CNX5.3, IC3.2 (QC), R9.2
/XEN6: CNX6.3, IC3.3 (QD), R10.2
/XEN7: IC3.4 (QE)
/XEN8: IC3.5 (QF)
/YA.0: CNY1.9, CNY2.9, IC1.15 (QA)
/YA.1: CNY1.8, CNY2.8, IC1.1 (QB)
/YA.2: CNY1.10, CNY2.10, IC1.2 (QC)
/YB.0: CNY1.2, CNY2.2, IC1.3 (QD)
/YB.1: CNY1.1, CNY2.1, IC1.4 (QE)
/YDAT: CNY1.4, CNY2.4, IC1.5 (QF)
/YEN1: CNY1.3, IC1.6 (QG), R3.2
/YEN2: CNY2.3, IC1.7 (QH), R4.2
/YEN3: IC3.6 (QG)
/YEN4: IC3.7 (QH)
/~OE: CN1.2, IC1.13 (~OE), IC2.13 (~OE), IC3.13 (~OE), R2.1
/~SRCLR: CN1.4, IC1.10 (~SRCLR), IC2.10 (~SRCLR), IC3.10 (~SRCLR), R1.1
GND: C1.2, C2.2, C3.2, CN1.5, CNX1.6, CNX2.6, CNX3.6, CNX4.6, CNX5.6, CNX6.6, CNY1.6, CNY2.6, IC1.8 (GND), IC2.8 (GND), IC3.8 (GND), R3.1, R4.1, R5.1, R6.1, R7.1, R8.1, R9.1, R10.1
unnamed: IC1.9 (QH'), IC2.14 (SER)
unnamed: IC2.9 (QH'), IC3.14 (SER)

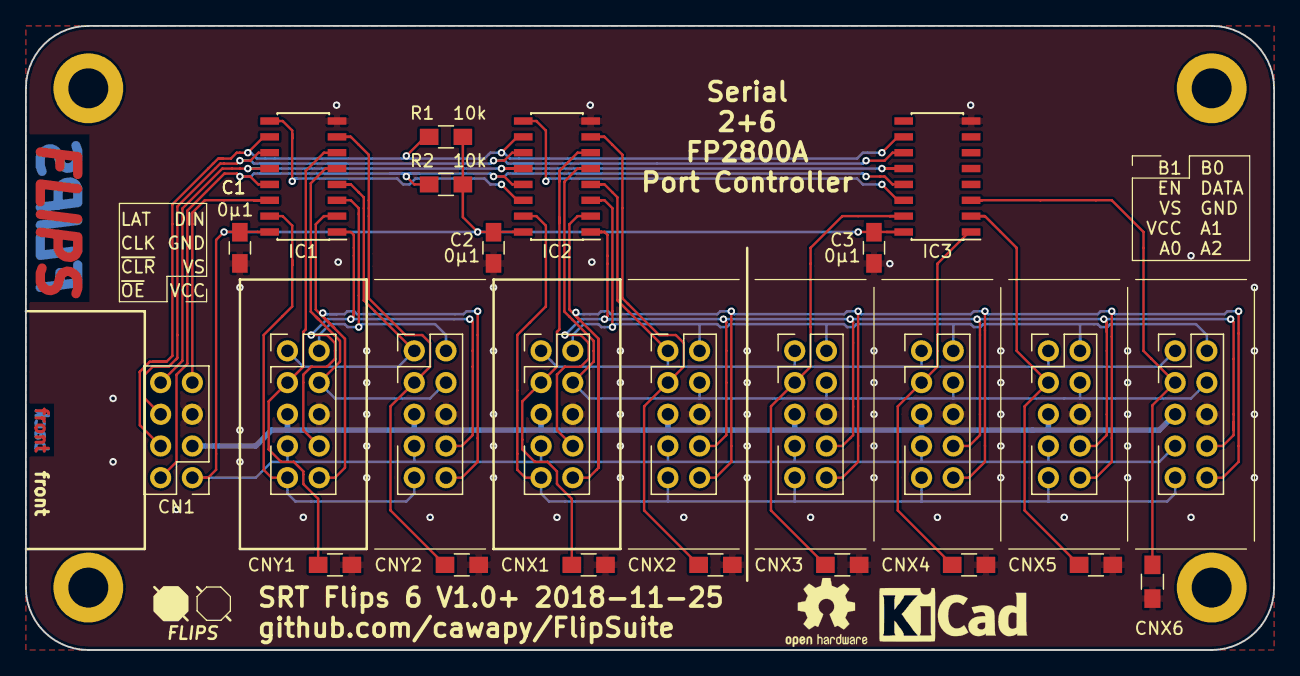
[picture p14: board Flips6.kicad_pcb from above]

Board: 2 copper layers, 100.0 x 50.0 mm, 25 parts (0 on the bottom side), 30 nets.

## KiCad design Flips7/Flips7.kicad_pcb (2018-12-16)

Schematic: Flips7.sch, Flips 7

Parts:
BOARD1: Conn_02x30_Top_Bottom; Pin_Header_Straight_Shrouded_2x30_Pitch2.54mm_AltNumbering
C1, C2, C3: 0µ1; C_0805_HandSoldering
CNX1: UFP2810; Pin_Header_Angle_Shrouded_2x05_Pitch2.54mm_ConvNumbering
CNY1, CNY2: UFP2810; Pin_Header_Angle_Shrouded_2x05_Pitch2.54mm_ConvNumbering
IC1, IC2, IC3: FP2800A; DIP-40_W15.24mm_Socket
JP1: Jumper_Cross; Cross_Jumper_2x2_2.54mm
R1, R2, R3: 10k; R_0805_HandSoldering
SHR1, SHR2: Conn_02x17_Odd_Even; Pin_Header_Straight_Shrouded_2x17_Pitch2.54mm_ConvNumbering

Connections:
/HV: CNX1.5, CNY1.5, CNY2.5, IC1.35, IC2.35, IC3.35
/RY01: BOARD1.18, IC1.36, SHR1.22, SHR2.22
/RY02: BOARD1.13, IC1.37, SHR1.24, SHR2.24
/RY03: BOARD1.9, IC1.38, SHR1.26, SHR2.26
/RY04: BOARD1.21, IC1.40, SHR1.30, SHR2.30
/RY05: BOARD1.24, IC1.34, SHR1.18, SHR2.18
/RY06: BOARD1.6, IC1.39, SHR1.28, SHR2.28
/RY07: BOARD1.3, IC1.33, SHR1.16, SHR2.16
/RY08: BOARD1.27, IC1.26, SHR1.2, SHR2.2
/RY09: BOARD1.30, IC1.27, SHR1.4, SHR2.4
/RY10: BOARD1.45, IC1.28, SHR1.6, SHR2.6
/RY11: BOARD1.58, IC1.29, SHR1.8, SHR2.8
/RY12: BOARD1.32, IC1.31, SHR1.12, SHR2.12
/RY13: BOARD1.37, IC1.30, SHR1.10, SHR2.10
/RY14: BOARD1.14, IC1.32, SHR1.14, SHR2.14
/RY15: BOARD1.52, IC2.36, SHR1.32, SHR2.32
/RY16: BOARD1.51, IC2.37, SHR1.34, SHR2.34
/VCC: C1.2, C2.1, C3.1, CNX1.7, CNY1.7, CNY2.7, IC1.17, IC2.17, IC3.17
/X01: BOARD1.35, IC3.16
/X02: BOARD1.34, IC3.15
/X03: BOARD1.33, IC3.14
/X04: IC3.13, JP1.4
/X04_NC: BOARD1.44, JP1.2
/X05: BOARD1.42, IC3.11
/X06: BOARD1.41, IC3.12
/X07: BOARD1.40, IC3.10
/X08: BOARD1.39, IC3.6
/X09: BOARD1.36, IC3.5
/X10: BOARD1.12, IC3.4
/X11: BOARD1.1, IC3.2
/X12: BOARD1.4, IC3.8
/X13: BOARD1.7, IC3.3
/X14: BOARD1.10, IC3.9
/X15: BOARD1.16, IC3.36
/X16: BOARD1.19, IC3.37
/X17: BOARD1.22, IC3.38
/X18: BOARD1.25, IC3.40
/X19: BOARD1.28, IC3.34
/X20: BOARD1.59, IC3.39
/X21: BOARD1.57, IC3.33
/X22: BOARD1.50, IC3.26
/X23: BOARD1.48, IC3.27
/X24: BOARD1.47, IC3.28
/X25: BOARD1.46, IC3.29
/X26: BOARD1.56, IC3.31
/X27: IC3.30, JP1.1
/X27_X04: BOARD1.55, JP1.3
/X28: BOARD1.54, IC3.32
/X.A0: CNX1.9, IC3.19
/X.A1: CNX1.8, IC3.18
/X.A2: CNX1.10, IC3.20
/X.B0: CNX1.2, IC3.21
/X.B1: CNX1.1, IC3.22
/X.EN: CNX1.3, IC3.24, R3.1
/X.POL: CNX1.4, IC3.23
/Y1.A0: CNY1.9, IC1.19
/Y1.A1: CNY1.8, IC1.18
/Y1.A2: CNY1.10, IC1.20
/Y1.B0: CNY1.2, IC1.21
/Y1.B1: CNY1.1, IC1.22
/Y1.EN: CNY1.3, IC1.24, R1.1
/Y1.POL: CNY1.4, IC1.23
/Y2.A0: CNY2.9, IC2.19
/Y2.A1: CNY2.8, IC2.18
/Y2.A2: CNY2.10, IC2.20
/Y2.B0: CNY2.2, IC2.21
/Y2.B1: CNY2.1, IC2.22
/Y2.EN: CNY2.3, IC2.24, R2.1
/Y2.POL: CNY2.4, IC2.23
/~SY01: BOARD1.17, IC1.16, SHR1.1, SHR2.1
/~SY02: BOARD1.11, IC1.15, SHR1.3, SHR2.3
/~SY03: BOARD1.8, IC1.14, SHR1.5, SHR2.5
/~SY04: BOARD1.20, IC1.13, SHR1.7, SHR2.7
/~SY05: BOARD1.23, IC1.11, SHR1.11, SHR2.11
/~SY06: BOARD1.5, IC1.12, SHR1.9, SHR2.9
/~SY07: BOARD1.2, IC1.10, SHR1.13, SHR2.13
/~SY08: BOARD1.26, IC1.6, SHR1.21, SHR2.21
/~SY09: BOARD1.29, IC1.5, SHR1.23, SHR2.23
/~SY10: BOARD1.43, IC1.4, SHR1.25, SHR2.25
/~SY11: BOARD1.60, IC1.2, SHR1.29, SHR2.29
/~SY12: BOARD1.31, IC1.8, SHR1.17, SHR2.17
/~SY13: BOARD1.38, IC1.3, SHR1.27, SHR2.27
/~SY14: BOARD1.15, IC1.9, SHR1.15, SHR2.15
/~SY15: BOARD1.53, IC2.16, SHR1.31, SHR2.31
/~SY16: BOARD1.49, IC2.15, SHR1.33, SHR2.33
GND: C1.1, C2.2, C3.2, CNX1.6, CNY1.6, CNY2.6, IC1.7, IC1.25, IC2.7, IC2.25, IC3.7, IC3.25, R1.2, R2.2, R3.2, SHR1.19, SHR1.20, SHR2.19, SHR2.20

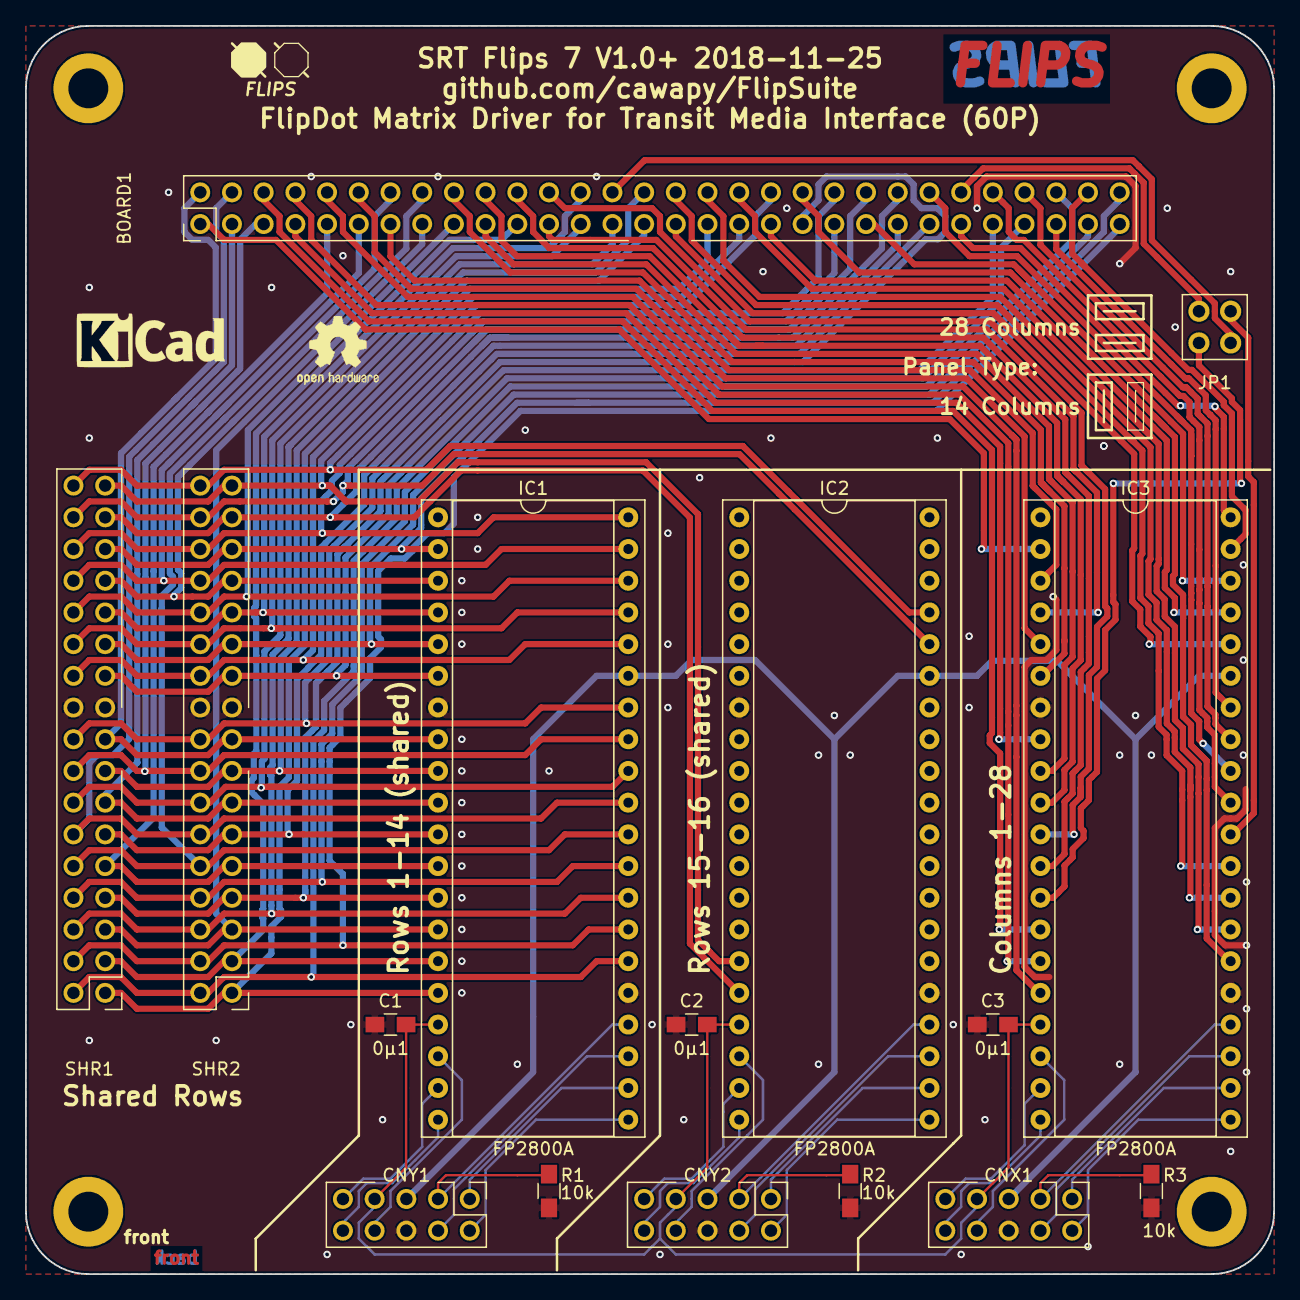
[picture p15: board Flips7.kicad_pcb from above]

Board: 2 copper layers, 100.0 x 100.0 mm, 16 parts (0 on the bottom side), 86 nets.

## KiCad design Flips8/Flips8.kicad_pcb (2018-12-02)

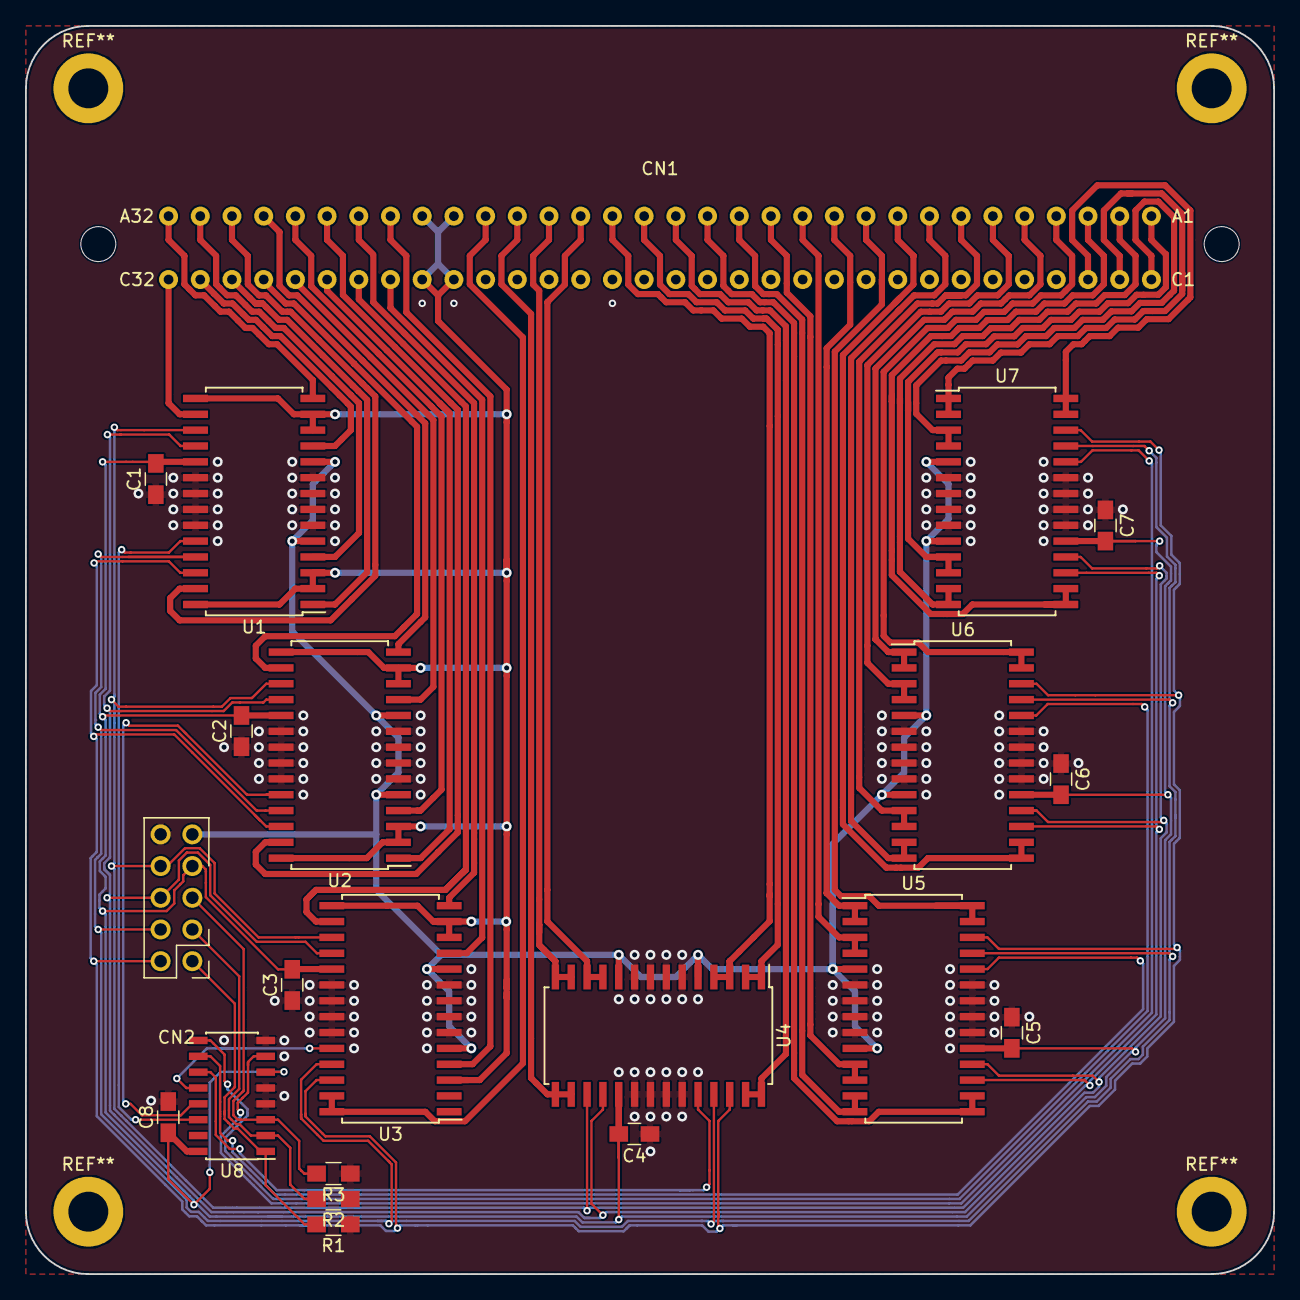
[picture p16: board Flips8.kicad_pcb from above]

Board: 2 copper layers, 100.0 x 100.0 mm, 21 parts (0 on the bottom side), 59 nets.

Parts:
C1, C2, C3, C4, C5, C6, C7, C8: 0μ1; C_0805_HandSoldering
CN1: Conn_02x32_Row_Letter_First_A_C; Annax-Connector
CN2: Conn_02x05_Odd_Even; Pin_Header_Angle_Shrouded_2x05_Pitch2.54mm_ConvNumbering
R1, R2, R3: 10k; R_0805_HandSoldering
U1, U2, U3, U4, U5, U6, U7: NCV7708; SOIC-28W_7.5x17.9mm_Pitch1.27mm
U8: 74LS138; SOIC-16_3.9x9.9mm_Pitch1.27mm

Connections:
+12V: CN2.9, U1.5, U1.10, U2.5, U2.10, U3.5, U3.10, U4.5, U4.10, U5.5, U5.10, U6.5, U6.10, U7.5, U7.10
/CSA0: CN2.1, R1.2, U8.1
/CSA1: CN2.3, R2.2, U8.2
/CSA2: CN2.5, R3.2, U8.3
/EN: CN2.8, U1.17, U2.17, U3.17, U4.17, U5.17, U6.17, U7.17
/RY: CN1.A23, CN1.A24, CN1.C23, CN1.C24, U1.2, U1.3, U1.12, U1.13, U1.15, U1.28, U2.2, U2.3, U2.12, U2.13, U2.15, U2.28, U3.3, U3.12, U3.13, U3.15
/SCLK: CN2.4, U1.25, U2.25, U3.25, U4.25, U5.25, U6.25, U7.25
/SI: CN2.2, U1.26, U2.26, U3.26, U4.26, U5.26, U6.26, U7.26
/SO: CN2.6, U1.18, U2.18, U3.18, U4.18, U5.18, U6.18, U7.18
/X1: CN1.A22, U3.27, U3.28
/X2: CN1.A21, U4.15, U4.16
/X3: CN1.A20, U4.13, U4.14
/X4: CN1.A19, U4.11, U4.12
/X5: CN1.A18, U4.3, U4.4
/X6: CN1.A17, U4.1, U4.2
/X7: CN1.A16, U4.27, U4.28
/X8: CN1.A15, U5.15, U5.16
/X9: CN1.A14, U5.13, U5.14
/X10: CN1.A13, U5.11, U5.12
/X11: CN1.A12, U5.3, U5.4
/X12: CN1.A11, U5.1, U5.2
/X13: CN1.A10, U5.27, U5.28
/X14: CN1.A9, U6.15, U6.16
/X15: CN1.A8, U6.13, U6.14
/X16: CN1.A7, U6.11, U6.12
/X17: CN1.A6, U6.3, U6.4
/X18: CN1.A5, U6.1, U6.2
/X19: CN1.A4, U6.27, U6.28
/X20: CN1.A3, U7.15, U7.16
/X21: CN1.A2, U7.13, U7.14
/X22: CN1.A1, U7.11, U7.12
/X23: CN1.C1, U7.3, U7.4
/X24: CN1.C2, U7.1, U7.2
/X25: CN1.C3, U7.27, U7.28
/~CS1: U1.24, U8.14
/~CS2: U2.24, U8.13
/~CS3: U3.24, U8.12
/~CS4: U4.24, U8.11
/~CS5: U5.24, U8.10
/~CS6: U6.24, U8.9
/~CS7: U7.24, U8.7
/~SY1: CN1.C32, U1.16
/~SY2: CN1.A32, U1.14
/~SY3: CN1.C31, U1.11
/~SY4: CN1.A31, U1.4
/~SY5: CN1.C30, U1.1
/~SY6: CN1.A30, U1.27
/~SY7: CN1.C29, U2.16
/~SY8: CN1.A29, U2.14
/~SY9: CN1.C28, U2.11
/~SY10: CN1.A28, U2.4
/~SY11: CN1.C27, U2.1
/~SY12: CN1.A27, U2.27
/~SY13: CN1.C26, U3.16
/~SY14: CN1.A26, U3.14
/~SY15: CN1.C25, U3.11
/~SY16: CN1.A25, U3.4
GND: C1.1, C2.1, C3.1, C4.1, C5.1, C6.1, C7.1, C8.2, CN2.10, R1.1, R2.1, R3.1, U1.6, U1.7, U1.8, U1.9, U1.20, U1.21, U1.22, U1.23, U2.6, U2.7, U2.8, U2.9, U2.20, U2.21, U2.22, U2.23, U3.6, U3.7, U3.8, U3.9, U3.20, U3.21, U3.22, U3.23, U4.6, U4.7, U4.8, U4.9, U4.20, U4.21, U4.22, U4.23, U5.6, U5.7, U5.8, U5.9, U5.20, U5.21, U5.22, U5.23, U6.6, U6.7, U6.8, U6.9, U6.20, U6.21, U6.22, U6.23, U7.6, U7.7, U7.8, U7.9, U7.20, U7.21, U7.22, U7.23, U8.4, U8.5, U8.8
VCC: C1.2, C2.2, C3.2, C4.2, C5.2, C6.2, C7.2, C8.1, CN2.7, U1.19, U2.19, U3.19, U4.19, U5.19, U6.19, U7.19, U8.6, U8.16

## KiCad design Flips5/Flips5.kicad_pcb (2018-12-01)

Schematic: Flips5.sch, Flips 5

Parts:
BRDIC1: Conn_02x17_Odd_Even; Pin_Header_Angle_Shrouded_2x17_Pitch2.54mm_ConvNumbering
BROSE20: Conn_02x10_Odd_Even; Pin_Header_Straight_Shrouded_2x10_Pitch2.54mm_ConvNumbering
BROSE34: Conn_02x17_Odd_Even; Pin_Header_Angle_Shrouded_2x17_Pitch2.54mm_ConvNumbering
BROSE60: Conn_02x30_Odd_Even; Pin_Header_Straight_Shrouded_2x30_Pitch2.54mm_ConvNumbering
C1, C2, C3: 0μ1; C_0805_HandSoldering
CNX1: UFP2810; Pin_Header_Angle_Shrouded_2x05_Pitch2.54mm
CNY1, CNY2: UFP2810; Pin_Header_Angle_Shrouded_2x05_Pitch2.54mm
IC1, IC2, IC3: FP2800A; DIP-40_W15.24mm_Socket
R1, R2, R3: 10k; R_0805_HandSoldering

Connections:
/GND: C1.1, C2.2, C3.2, CNX1.6, CNY1.6, CNY2.6, IC1.7, IC1.25, IC2.7, IC2.25, IC3.7, IC3.25, R1.1, R2.1, R3.1
/HV: CNX1.5, CNY1.5, CNY2.5, IC1.35, IC2.35, IC3.35
/SY1: BROSE34.19, BROSE60.1, IC1.16
/SY2: BROSE34.21, BROSE60.2, IC1.15
/SY3: BROSE34.23, BROSE60.3, IC1.14
/SY4: BROSE34.25, BROSE60.4, IC1.13
/SY5: BROSE34.27, BROSE60.5, IC1.11
/SY6: BROSE34.29, BROSE60.6, IC1.12
/SY7: BROSE34.31, BROSE60.7, IC1.10
/SY8: BROSE60.8, IC1.6
/SY9: BROSE60.9, IC1.5
/SY10: BROSE60.10, IC1.4
/SY11: BROSE60.11, IC1.2
/SY12: BROSE60.12, IC1.8
/SY13: BROSE60.13, IC1.3
/SY14: BROSE60.14, IC1.9
/SY15: BROSE60.15, IC2.16
/SY16: BROSE60.16, IC2.15
/SY17: BROSE60.17, IC2.14
/SY18: BROSE60.18, IC2.13
/SY19: BROSE60.19, IC2.11
/SY20: BROSE60.20, IC2.12
/SY21: BROSE20.1, IC2.10
/SY22: BROSE20.2, IC2.6
/SY23: BROSE20.3, IC2.5
/SY24: BROSE20.4, IC2.4
/SY25: BROSE20.5, IC2.2
/SY26: BROSE20.6, IC2.8
/SY27: BROSE20.7, IC2.3
/SY28: BROSE20.8, IC2.9
/VCC: C1.2, C2.1, C3.1, CNX1.7, CNY1.7, CNY2.7, IC1.17, IC2.17, IC3.17
/X1: BRDIC1.32, IC3.16
/X2: BRDIC1.30, IC3.15
/X3: BRDIC1.28, IC3.14
/X4: BRDIC1.26, IC3.13
/X5: BRDIC1.22, IC3.11
/X6: BRDIC1.24, IC3.12
/X7: BRDIC1.20, IC3.10
/X8: BRDIC1.12, IC3.6
/X9: BRDIC1.10, IC3.5
/X10: BRDIC1.8, IC3.4
/X11: BRDIC1.4, IC3.2
/X12: BRDIC1.16, IC3.8
/X13: BRDIC1.6, IC3.3
/X14: BRDIC1.18, IC3.9
/X15: BRDIC1.9, IC3.36
/X16: BRDIC1.7, IC3.37
/X17: BRDIC1.5, IC3.38
/X18: BRDIC1.1, IC3.40
/X19: BRDIC1.13, IC3.34
/X20: BRDIC1.3, IC3.39
/X21: BRDIC1.15, IC3.33
/X22: BRDIC1.29, IC3.26
/X23: BRDIC1.27, IC3.27
/X24: BRDIC1.25, IC3.28
/X25: BRDIC1.23, IC3.29
/X26: BRDIC1.19, IC3.31
/X27: BRDIC1.21, IC3.30
/X28: BRDIC1.17, IC3.32
/X.A0: CNX1.9, IC3.19
/X.A1: CNX1.8, IC3.18
/X.A2: CNX1.10, IC3.20
/X.B0: CNX1.2, IC3.21
/X.B1: CNX1.1, IC3.22
/X.EN: CNX1.3, IC3.24, R3.2
/X.POL: CNX1.4, IC3.23
/Y1.A0: CNY1.9, IC1.19
/Y1.A1: CNY1.8, IC1.18
/Y1.A2: CNY1.10, IC1.20
/Y1.B0: CNY1.2, IC1.21
/Y1.B1: CNY1.1, IC1.22
/Y1.EN: CNY1.3, IC1.24, R1.2
/Y1.POL: CNY1.4, IC1.23
/Y2.A0: CNY2.9, IC2.19
/Y2.A1: CNY2.8, IC2.18
/Y2.A2: CNY2.10, IC2.20
/Y2.B0: CNY2.2, IC2.21
/Y2.B1: CNY2.1, IC2.22
/Y2.EN: CNY2.3, IC2.24, R2.2
/Y2.POL: CNY2.4, IC2.23
/~RY1: BROSE34.20, BROSE60.21, IC1.36
/~RY2: BROSE34.22, BROSE60.22, IC1.37
/~RY3: BROSE34.24, BROSE60.23, IC1.38
/~RY4: BROSE34.26, BROSE60.24, IC1.40
/~RY5: BROSE34.28, BROSE60.25, IC1.34
/~RY6: BROSE34.30, BROSE60.26, IC1.39
/~RY7: BROSE34.32, BROSE60.27, IC1.33
/~RY8: BROSE60.28, IC1.26
/~RY9: BROSE60.29, IC1.27
/~RY10: BROSE60.30, IC1.28
/~RY11: BROSE60.31, IC1.29
/~RY12: BROSE60.32, IC1.31
/~RY13: BROSE60.33, IC1.30
/~RY14: BROSE60.34, IC1.32
/~RY15: BROSE60.35, IC2.36
/~RY16: BROSE60.36, IC2.37
/~RY17: BROSE60.37, IC2.38
/~RY18: BROSE60.38, IC2.40
/~RY19: BROSE60.39, IC2.34
/~RY20: BROSE60.40, IC2.39
/~RY21: BROSE20.9, IC2.33
/~RY22: BROSE20.10, IC2.26
/~RY23: BROSE20.11, IC2.27
/~RY24: BROSE20.12, IC2.28
/~RY25: BROSE20.13, IC2.29
/~RY26: BROSE20.14, IC2.31
/~RY27: BROSE20.15, IC2.30
/~RY28: BROSE20.16, IC2.32

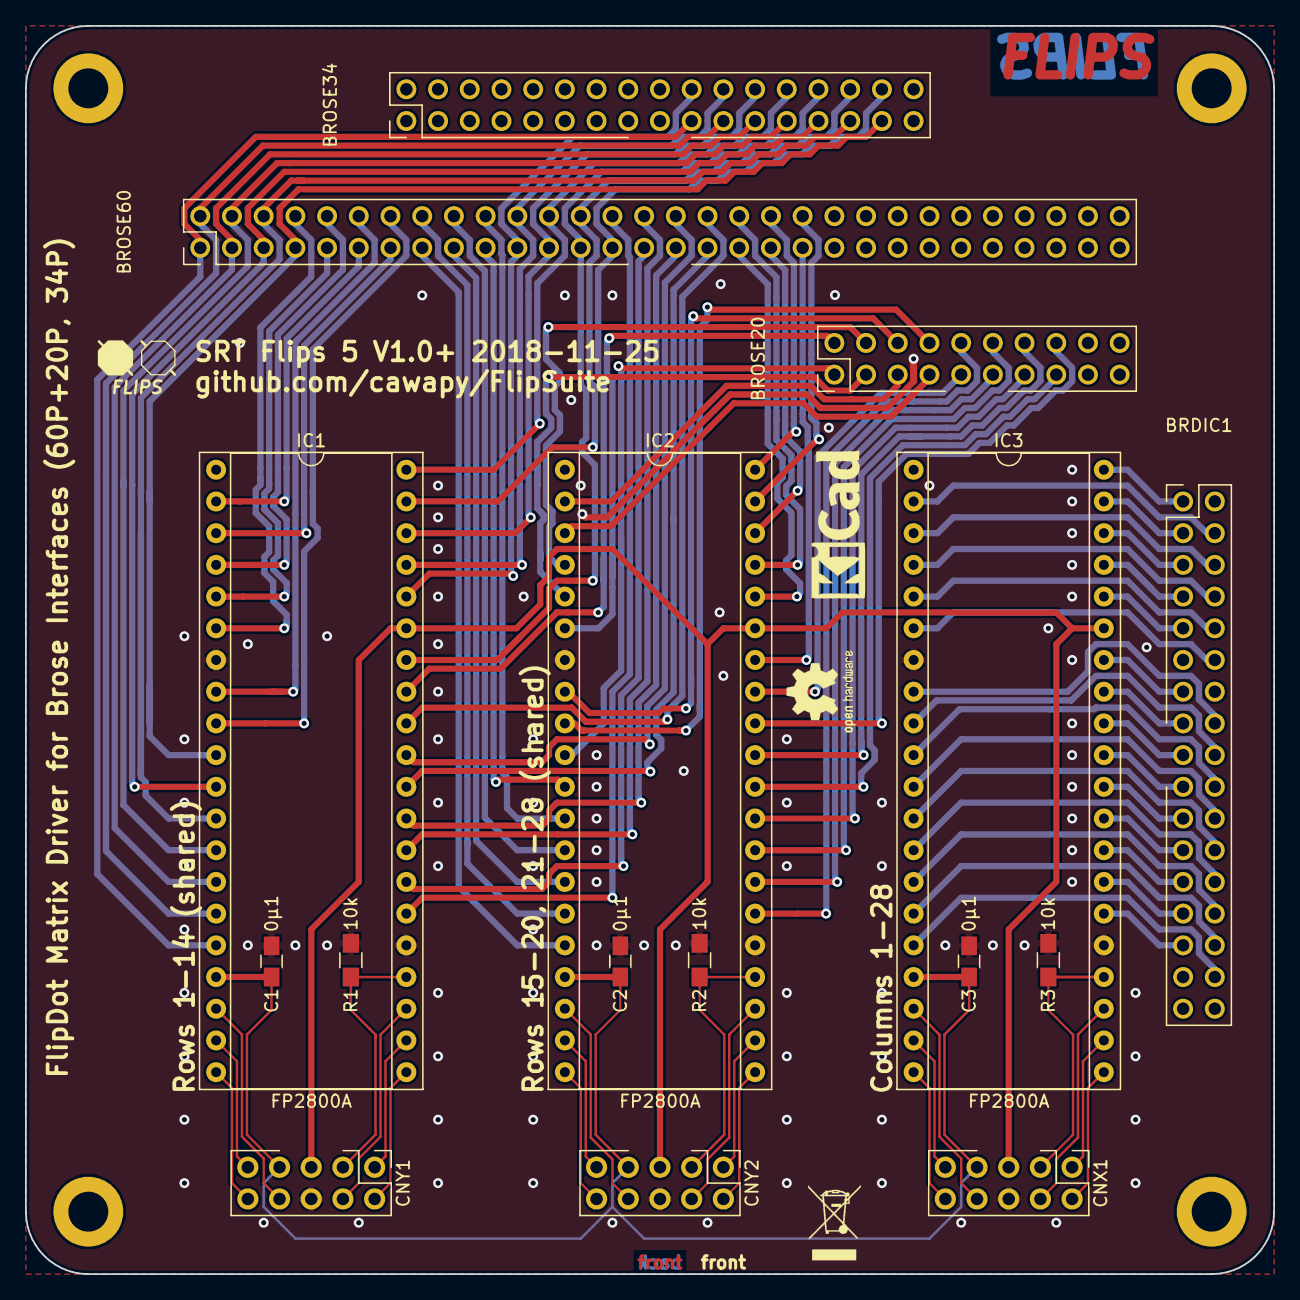
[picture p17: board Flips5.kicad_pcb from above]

Board: 2 copper layers, 100.0 x 100.0 mm, 16 parts (0 on the bottom side), 108 nets.

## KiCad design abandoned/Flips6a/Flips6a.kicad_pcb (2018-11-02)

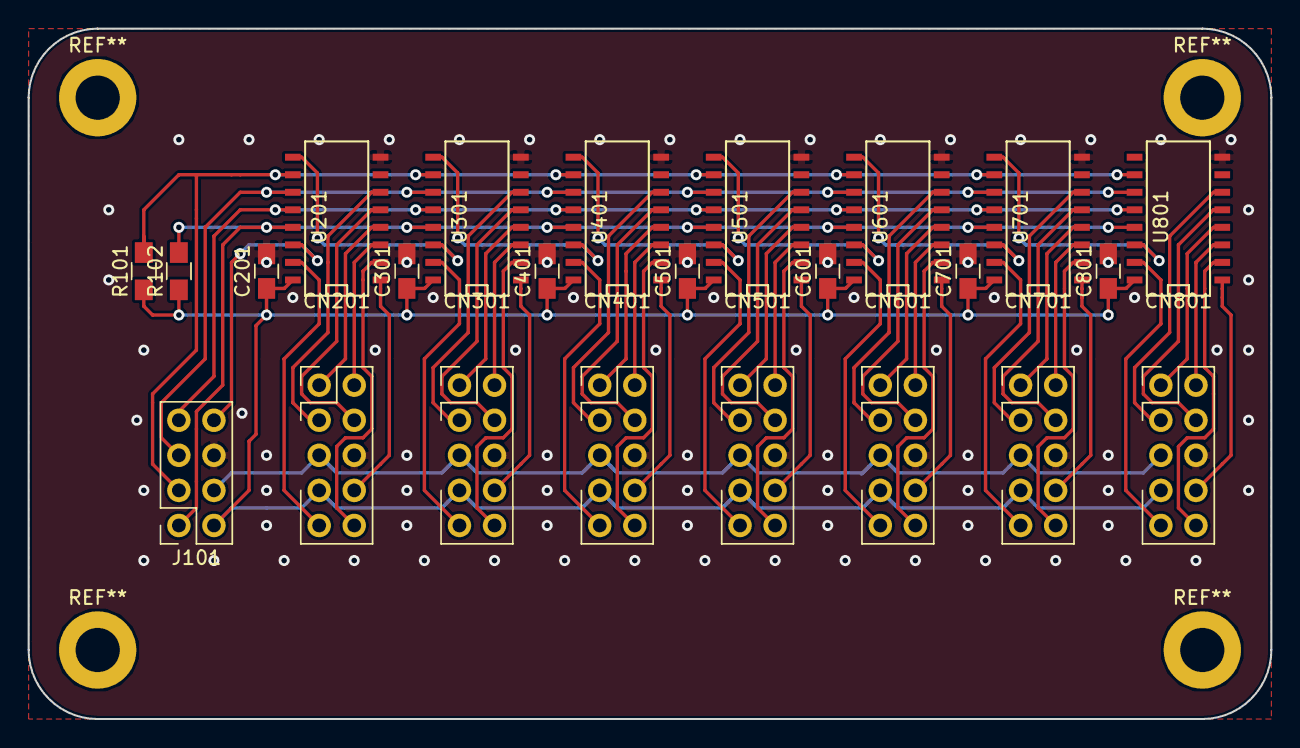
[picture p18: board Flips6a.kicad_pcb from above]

Board: 2 copper layers, 90.0 x 50.0 mm, 24 parts (0 on the bottom side), 63 nets.

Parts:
C201, C301, C401, C501, C601, C701, C801: 0u1; C_0805_HandSoldering
CN201, CN301, CN401, CN501, CN601, CN701, CN801: UFP2810; Pin_Header_Straight_Shrouded_2x05_Pitch2.54mm
J101: Conn_02x04_Odd_Even; Socket_Strip_Straight_2x04_Pitch2.54mm
R101, R102: 10K; R_0805_HandSoldering
U201, U301, U401, U501, U601, U701, U801: 74HCT595; SO-16-N

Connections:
+5V: C201.1, C301.1, C401.1, C501.1, C601.1, C701.1, C801.1, CN201.7, CN301.7, CN401.7, CN501.7, CN601.7, CN701.7, CN801.7, J101.2, R101.1, R102.1, U201.16, U301.16, U401.16, U501.16, U601.16, U701.16, U801.16
+12V: CN201.5, CN301.5, CN401.5, CN501.5, CN601.5, CN701.5, CN801.5, J101.4
/ShiftRegister2/A0: CN201.9, U201.15
/ShiftRegister2/A1: CN201.8, U201.1
/ShiftRegister2/A2: CN201.10, U201.2
/ShiftRegister2/B0: CN201.2, U201.3
/ShiftRegister2/B1: CN201.1, U201.4
/ShiftRegister2/DATA: CN201.4, U201.5
/ShiftRegister2/DIN: J101.8, U201.14
/ShiftRegister2/EN: CN201.3, U201.6
/ShiftRegister3/A0: CN301.9, U301.15
/ShiftRegister3/A1: CN301.8, U301.1
/ShiftRegister3/A2: CN301.10, U301.2
/ShiftRegister3/B0: CN301.2, U301.3
/ShiftRegister3/B1: CN301.1, U301.4
/ShiftRegister3/DATA: CN301.4, U301.5
/ShiftRegister3/DIN: U201.9, U301.14
/ShiftRegister3/EN: CN301.3, U301.6
/ShiftRegister4/A0: CN401.9, U401.15
/ShiftRegister4/A1: CN401.8, U401.1
/ShiftRegister4/A2: CN401.10, U401.2
/ShiftRegister4/B0: CN401.2, U401.3
/ShiftRegister4/B1: CN401.1, U401.4
/ShiftRegister4/DATA: CN401.4, U401.5
/ShiftRegister4/DIN: U301.9, U401.14
/ShiftRegister4/EN: CN401.3, U401.6
/ShiftRegister5/A0: CN501.9, U501.15
/ShiftRegister5/A1: CN501.8, U501.1
/ShiftRegister5/A2: CN501.10, U501.2
/ShiftRegister5/B0: CN501.2, U501.3
/ShiftRegister5/B1: CN501.1, U501.4
/ShiftRegister5/DATA: CN501.4, U501.5
/ShiftRegister5/DIN: U401.9, U501.14
/ShiftRegister5/EN: CN501.3, U501.6
/ShiftRegister6/A0: CN601.9, U601.15
/ShiftRegister6/A1: CN601.8, U601.1
/ShiftRegister6/A2: CN601.10, U601.2
/ShiftRegister6/B0: CN601.2, U601.3
/ShiftRegister6/B1: CN601.1, U601.4
/ShiftRegister6/DATA: CN601.4, U601.5
/ShiftRegister6/DIN: U501.9, U601.14
/ShiftRegister6/EN: CN601.3, U601.6
/ShiftRegister7/A0: CN701.9, U701.15
/ShiftRegister7/A1: CN701.8, U701.1
/ShiftRegister7/A2: CN701.10, U701.2
/ShiftRegister7/B0: CN701.2, U701.3
/ShiftRegister7/B1: CN701.1, U701.4
/ShiftRegister7/DATA: CN701.4, U701.5
/ShiftRegister7/DIN: U601.9, U701.14
/ShiftRegister7/EN: CN701.3, U701.6
/ShiftRegister8/A0: CN801.9, U801.15
/ShiftRegister8/A1: CN801.8, U801.1
/ShiftRegister8/A2: CN801.10, U801.2
/ShiftRegister8/B0: CN801.2, U801.3
/ShiftRegister8/B1: CN801.1, U801.4
/ShiftRegister8/DATA: CN801.4, U801.5
/ShiftRegister8/DIN: U701.9, U801.14
/ShiftRegister8/EN: CN801.3, U801.6
GND: C201.2, C301.2, C401.2, C501.2, C601.2, C701.2, C801.2, CN201.6, CN301.6, CN401.6, CN501.6, CN601.6, CN701.6, CN801.6, J101.6, U201.8, U301.8, U401.8, U501.8, U601.8, U701.8, U801.8
RCLK: J101.7, U201.12, U301.12, U401.12, U501.12, U601.12, U701.12, U801.12
SRCLK: J101.5, U201.11, U301.11, U401.11, U501.11, U601.11, U701.11, U801.11
~OE: J101.1, R102.2, U201.13, U301.13, U401.13, U501.13, U601.13, U701.13, U801.13
~SRCLR: J101.3, R101.2, U201.10, U301.10, U401.10, U501.10, U601.10, U701.10, U801.10

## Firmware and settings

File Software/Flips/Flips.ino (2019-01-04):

#include <SPI.h>

#include "tpluc/Timespan.h"
#include "tpluc/DigitalOutput.h"
#include "tpluc/ArduinoApiSpi.h"
#include "tpluc/ShiftRegister595SpiConnected.h"

#include "Flips6.h"

typedef tpluc::Arduino::DigitalOutput<8> ShiftRegisterRsPin;
typedef tpluc::Arduino::DigitalOutput<9> ShiftRegisterOePin;
typedef tpluc::Arduino::DigitalOutput<10> ShiftRegisterCsPin;

typedef tpluc::ArduinoApi::Spi<> Spi;

typedef ShiftRegister595SpiConnected<ShiftRegisterCsPin, ShiftRegisterOePin, ShiftRegisterRsPin, Spi> ShiftRegister;
typedef Flips6<ShiftRegister> flips6;

struct Adapter
{
    void Set(uint8_t x, uint8_t y, bool value)
    {
        flips6::Pulse(y, x, value);
    }
};

template<uint16_t w, uint16_t h, typename Underlying> class MonoBuffer
{
private:
    Underlying& underlying;
    static const uint16_t memSize = ((w*h) + 7) / 8;
    uint8_t mem[memSize];
public:
    MonoBuffer(Underlying& underlying) :
        underlying(underlying)
    {
    }

    void SetAll(bool value, bool force = false)
    {
        for (uint8_t x = 0; x < w; x++)
        {
            for (uint8_t y = 0; y < h; y++)
            {
                Set(x, y, value, force);
            }
        }
    }

    void Set(uint8_t x, uint8_t y, bool value)
    {
        Set(x, y, value, false);
    }
private:

    void Set(uint8_t x, uint8_t y, bool value, bool force)
    {
        if (Update(x, y, value) || force)
        {
            underlying.Set(x, y, value);
        }
    }

    bool Update(uint8_t x, uint8_t y, bool newVal)
    {
        uint16_t bitAddr = x * h + y;
        uint16_t byteAddr = bitAddr / 8;
        uint8_t bitPos = bitAddr % 8;

        if (byteAddr >= memSize) return false;

        uint8_t& byteRef = mem[byteAddr];
        uint8_t bit = 1 << bitPos;
        bool oldVal = (byteRef & bit) != 0;
        if (oldVal == newVal) return false;

        if (newVal)
            byteRef |= bit;
        else
            byteRef &= ~bit;
        return true;
    }
};

Adapter adapter;
MonoBuffer<25, 7, Adapter> buffer(adapter);

void setup()
{
    Spi::Init();
    ShiftRegister::Init();
    buffer.SetAll(false, true);
}

void WriteColumn7(uint8_t x, uint8_t colBitmap)
{
    for (uint8_t y = 0; y < 7; y++)
    {
        buffer.Set(x, y, (colBitmap & (1 << y)) != 0);
    }
}

void WriteMatrix5x7(uint8_t x0, uint8_t col1bitmap, uint8_t col2bitmap, uint8_t col3bitmap, uint8_t col4bitmap, uint8_t col5bitmap)
{
    WriteColumn7(x0 + 0, col1bitmap);
    WriteColumn7(x0 + 1, col2bitmap);
    WriteColumn7(x0 + 2, col3bitmap);
    WriteColumn7(x0 + 3, col4bitmap);
    WriteColumn7(x0 + 4, col5bitmap);
}

void WriteDigit(uint8_t digitNumber, uint8_t col0bitmap, uint8_t col1bitmap, uint8_t col2bitmap, uint8_t col3bitmap, uint8_t col4bitmap)
{
    WriteMatrix5x7(5 * digitNumber, col0bitmap, col1bitmap, col2bitmap, col3bitmap, col4bitmap);
}

#define DEF_LETTER(name,u0,u1,u2,u3,u4) static const uint8_t name[5] = { (u0),(u1),(u2),(u3),(u4) };

DEF_LETTER(CYR_v,
    0b0000000,
    0b0111110,
    0b0101010,
    0b0101010,
    0b0010100);

DEF_LETTER(LAT_a,
    0b0000000,
    0b0010000,
    0b0101010,
    0b0101010,
    0b0111100);

DEF_LETTER(CYR_d,
    0b1100000,
    0b0111100,
    0b0100010,
    0b0111110,
    0b1100000);

DEF_LETTER(CYR_i,
    0b0000000,
    0b0111110,
    0b0001000,
    0b0000100,
    0b0111110);

DEF_LETTER(CYR_m,
    0b0111110,
    0b0000100,
    0b0001000,
    0b0000100,
    0b0111110);

DEF_LETTER(LAT_C,
    0b0011110,
    0b0100001,
    0b0100001,
    0b0100001,
    0b0010010);

DEF_LETTER(CYR_n,
    0b0000000,
    0b0111110,
    0b0001000,
    0b0001000,
    0b0111110);

DEF_LETTER(LAT_o,
    0b0000000,
    0b0011100,
    0b0100010,
    0b0100010,
    0b0011100);

DEF_LETTER(CYR_y,
    0b0111110,
    0b0101000,
    0b0010000,
    0b0000000,
    0b0111110);

DEF_LETTER(BLK,
    0b0000000,
    0b0000000,
    0b0000000,
    0b0000000,
    0b0000000);

DEF_LETTER(CYR_g,
    0b0000000,
    0b0111110,
    0b0000010,
    0b0000010,
    0b0000010);

DEF_LETTER(CYR_t,
    0b0000000,
    0b0000010,
    0b0111110,
    0b0000010,
    0b0000000);

DEF_LETTER(CYR_sch,
    0b0111110,
    0b0100000,
    0b0111110,
    0b0100000,
    0b0111110);

DEF_LETTER(DIG_2,
    0b0100010,
    0b0110011,
    0b0111001,
    0b0101111,
    0b0100110
    );

DEF_LETTER(DIG_0,
    0b0011110,
    0b0111111,
    0b0100001,
    0b0111111,
    0b0011110);

DEF_LETTER(DIG_1,
    0b0000000,
    0b0000010,
    0b0111111,
    0b0111111,
    0b0000000);

DEF_LETTER(DIG_9,
    0b0000110,
    0b0101111,
    0b0101001,
    0b0111111,
    0b0011110);

DEF_LETTER(SYM_EXCLAM,
    0b0000000,
    0b0000000,
    0b0101111,
    0b0000000,
    0b0000000);

void WriteScreen(const uint8_t* digit0Bitmap, const uint8_t* digit1Bitmap, const uint8_t* digit2Bitmap, const uint8_t* digit3Bitmap, const uint8_t* digit4Bitmap)
{
    WriteDigit(0, digit0Bitmap[0], digit0Bitmap[1], digit0Bitmap[2], digit0Bitmap[3], digit0Bitmap[4]);
    WriteDigit(1, digit1Bitmap[0], digit1Bitmap[1], digit1Bitmap[2], digit1Bitmap[3], digit1Bitmap[4]);
    WriteDigit(2, digit2Bitmap[0], digit2Bitmap[1], digit2Bitmap[2], digit2Bitmap[3], digit2Bitmap[4]);
    WriteDigit(3, digit3Bitmap[0], digit3Bitmap[1], digit3Bitmap[2], digit3Bitmap[3], digit3Bitmap[4]);
    WriteDigit(4, digit4Bitmap[0], digit4Bitmap[1], digit4Bitmap[2], digit4Bitmap[3], digit4Bitmap[4]);
}

void loop()
{
    buffer.SetAll(false);

    tpluc::TimespanMs<2500>::Wait();

    WriteScreen(BLK, BLK, LAT_C, BLK, BLK);

    tpluc::TimespanMs<1000>::Wait();

    WriteScreen(CYR_n, LAT_o, CYR_v, CYR_y, CYR_m);

    tpluc::TimespanMs<2500>::Wait();

    WriteScreen(CYR_g, LAT_o, CYR_d, LAT_o, CYR_m);

    tpluc::TimespanMs<2500>::Wait();

    WriteScreen(DIG_2, DIG_0, DIG_1, DIG_9, SYM_EXCLAM);

    tpluc::TimespanMs<2500>::Wait();

    WriteScreen(BLK, LAT_o, CYR_t, BLK, BLK);

    tpluc::TimespanMs<1000>::Wait();

    WriteScreen(LAT_C, LAT_a, CYR_sch, CYR_i, BLK);

    tpluc::TimespanMs<2500>::Wait();

    for (int y = 0; y < 7; y++)
    {
        bool even = y % 2 == 0;
        for (int x = even ? 0 : 24; even ? x < 25 : x >= 0; x += even ? 1 : -1)
        {
            buffer.Set(x, y, true);
            tpluc::TimespanMs<10>::Wait();
        }
    }

    tpluc::TimespanMs<500>::Wait();

    for (int x = 0; x < 25; x++)
    {
        bool even = x % 2 == 0;
        for (int y = even ? 0 : 6; even ? y < 7 : y >= 0; y += even ? 1 : -1)
        {
            buffer.Set(x, y, false);
            tpluc::TimespanMs<10>::Wait();
        }
    }
}

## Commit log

2018-08-27 Improve FPDriverPlug
    - Switch from DIP40 to DIP32
    - Use stronger traces for connections with relevant current
    - Use copper fill for GND
    [FPDriverPlug.kicad_pcb, FPDriverPlug.sch]
2018-08-27 Rework traces on FPDriverPlug
    - move non-GND traces to back layer
    - use direct non-45 degree traces for pass through connections
    [FPDriverPlug.kicad_pcb]
2018-08-27 changing 3d model to get illusion of dip40 socket
    [FPDriverPlug.kicad_pcb]
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2018-08-28 - Using DIP32 instead of DIP40 for FP2800A-Outputs - Shrinking Board to 80x55, re-aligning mounting holes to be in 5 mm raster - Labeling sheet and pcb plan - adding text and drawing on pcb
    [Brose60Adapter.kicad_pcb, Brose60Adapter.sch]
2018-08-29 adding project data to schematic and pcb
    [FPDriverPlug.kicad_pcb, FPDriverPlug.sch]
2018-08-29 removing leftover drawings on Eco2.User layer
    [FPDriverPlug.kicad_pcb]
2018-08-29 adding rudimentary labeling on copper layers
    [FPDriverPlug.kicad_pcb]
2018-10-28 0.2 of Flips4
    - Use IDC shrouded header
    - Add more space between IC and header
    - Center header
    - Remove round corners
    - Fix labels
    [FPDriverPlug.kicad_pcb]
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2018-10-28 shrinking Flips4 to minimum
    [FPDriverPlug.kicad_pcb]
2018-10-28 adding optional pulldown for ENABLE
    [FPDriverPlug.kicad_pcb, FPDriverPlug.sch]
2018-10-29 Using angled IDC connector
    [FPDriverPlug.kicad_pcb]
2018-10-29 Rework silkscreen
    [FPDriverPlug.kicad_pcb]
2018-10-29 adding Flips4 label to front
    [FPDriverPlug.kicad_pcb]
2018-10-29 Adding Flips6 project with schematic
    [Flips6.kicad_pcb, Flips6.sch, ShiftRegister.sch]
2018-10-29 switch resistor to 0805 package
    [FPDriverPlug.kicad_pcb, FPDriverPlug.sch]
2018-10-29 Switching to 0805 smd packages for Cs and Rs
    [Flips6.sch, ShiftRegister.sch]
2018-10-29 proper naming of active-low signals ~OE and ~SRCLR
    [Flips6.sch, ShiftRegister.sch]
2018-10-30 Adding first layout concept
    [Flips6.kicad_pcb]
2018-10-30 Finished routing for Fips6 first attempt
    [Flips6.kicad_pcb, Flips6.sch, ShiftRegister.sch]
2018-10-30 Making shape 90x50, with mounting holes in 80x40 rectangle
    [Flips6.kicad_pcb]
2018-10-31 adding vias for GND
    [Flips6.kicad_pcb]
2018-10-31 fixing path of Flips6
    [Flips6.kicad_pcb, Flips6.sch, ShiftRegister.sch]
2018-10-31 adding flips6b for 2x8 bit shift register control
    [Flips6b.kicad_pcb, Flips6b.sch, ShiftRegister.sch]
2018-10-31 first attempt of Flips6b
    [Flips6b.kicad_pcb, Flips6b.sch, ShiftRegister.sch]
2018-11-01 first attempt for Flips6b routed
    [Flips6b.kicad_pcb]
2018-11-01 adding vias to Flips6b
    [Flips6b.kicad_pcb]
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2018-11-01 Updating IDC connector 3d models
    [Flips6b.kicad_pcb]
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2018-11-01 adding Flips6c with schematics
    [Flips6c.kicad_pcb, Flips6c.sch]
2018-11-01 partial pcb layout / routing of Flips6c
    [Flips6c.kicad_pcb]
2018-11-01 Fixing wrong wiring of DIN/DOUT
    [Flips6c.sch]
2018-11-01 finish tracing PCB for flips6c
    [Flips6c.kicad_pcb]
2018-11-01 moving pullups into small gap, leaving space for text/labels
    [Flips6c.kicad_pcb]
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2018-11-01 rework silk screen
    [Flips6c.kicad_pcb]
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2018-11-01 renamed FPDriverPlug Flips4
    [Flips4.kicad_pcb, Flips4.sch]
2018-11-01 renamed Brose60Adapter to Flips5
    [Flips5.kicad_pcb, Flips5.sch]
2018-11-02 adding Flips5Plus
    [Flips5Plus.kicad_pcb, Flips5Plus.sch]
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2018-11-02 using ANGLED shrouded header
    [Flips5Plus.kicad_pcb, Flips5Plus.sch]
2018-11-02 using own UFP2810 connector
    [Flips4.kicad_pcb, Flips4.sch]
2018-11-02 flips 6c to use own UFP2810 connector
    [Flips6c.kicad_pcb, Flips6c.sch]
2018-11-02 switch flips 6a to use own UFP2810 connector
    [Flips6a.kicad_pcb, Flips6a.sch, ShiftRegister.sch]
2018-11-02 Flips6b use UFP2810 connector
    [Flips6b.kicad_pcb, Flips6b.sch]
2018-11-02 fixing 8 pin connector
    [Flips6c.kicad_pcb, Flips6c.sch]
2018-11-02 improve 595 control traces
    [Flips6c.kicad_pcb]
2018-11-02 improve 595 5v supply tracing
    [Flips6c.kicad_pcb]
2018-11-02 reworking gnd vias
    [Flips6c.kicad_pcb]
2018-11-02 adding logos and 3d models
    [Flips5Plus.kicad_pcb]
2018-11-03 rework inscriptions
    [Flips4.kicad_pcb]
2018-11-03 rearranging mounting holes and symbols fixing measurements
    [Flips5Plus.kicad_pcb]
2018-11-03 remove invalid mask line
    [Flips5Plus.kicad_pcb]
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2018-11-03 setting up for plot/export
    [Flips4.kicad_pcb, Flips5Plus.kicad_pcb, Flips6c.kicad_pcb]
2018-11-03 toggling copper behind "K" of "KiCad" logo
    [Flips4.kicad_pcb, Flips5Plus.kicad_pcb, Flips6c.kicad_pcb]
2018-11-03 set flip current traces to 0.5mm
    [Flips5Plus.kicad_pcb]
2018-11-03 made 12 V net .44 mm, but 5 V net standard 0.2 mm
    [Flips6c.kicad_pcb]
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2018-11-04 More FP2800 info printed on Flips4
    [Flips4.kicad_pcb]
2018-11-04 adding description and pinout
    [Flips6c.kicad_pcb]
2018-11-04 starting Flips7 for TransitMedia displays
    [Flips7.kicad_pcb, Flips7.sch]
2018-11-04 tracing flips7
    [Flips7.kicad_pcb]
2018-11-05 Using straight instead of angled IDC connector due to limited space on Brose display
    [Flips4.kicad_pcb, Flips4.sch]
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2018-11-06 fixing design rule to reflect new net names
    [Flips7.kicad_pcb]
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2018-11-06 cloning Flips5Plus from Flips5X
    [Flips5X.kicad_pcb, Flips5X.sch]
2018-11-06 introducing Flips5X concept
    [Flips5X.kicad_pcb, Flips5X.sch]
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2018-11-07 Using new 34P IDC connector for connecting column driver FP2800 onto display board
    [Flips5X.kicad_pcb, Flips5X.sch]
2018-11-07 adding 34P connector for 5x digit a 5x7 dots display
    [Flips5X.kicad_pcb, Flips5X.sch]
2018-11-10 new layout for FlipsX5
    [Flips5X.kicad_pcb]
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2018-11-10 writing 0μ1 instead of 0U1 for 0.1 micro farad
    [Flips5X.sch]
2018-11-10 adding R3 and 0μ1 value to PCB, including FP2800 values
    [Flips5X.kicad_pcb]
2018-11-10 rename L.* and R.* to Y1.* and Y2.*
    [Flips5X.kicad_pcb, Flips5X.sch]
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2018-11-10 fixing DIP connector assignment; adding vias
    [Flips5X.kicad_pcb, Flips5X.sch]
2018-11-10 adding flips6d based on flips6c
    [Flips6d.kicad_pcb, Flips6d.sch]
2018-11-11 Fixing 34 Pin interface pin mapping; renaming RYnn to ~RYnn
    [Flips5X.kicad_pcb, Flips5X.sch]
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2018-11-11 Fixing values to read more friendly, including tech agnostic 74595
    [Flips6c.kicad_pcb, Flips6c.sch]
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2018-11-12 new routing attempt (wip) for Flips7
    [Flips7.kicad_pcb, Flips7.sch]
2018-11-13 more tracing for Flips7 (still wip)
    [Flips7.kicad_pcb]
2018-11-13 Tracing column driver lines for Flips7
    [Flips7.kicad_pcb]
2018-11-13 single GND, VCC and HV; almost finish tracing
    [Flips7.kicad_pcb, Flips7.sch]
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2018-11-13 Fixing C values to 0µ1; connecting VCC of 3 units
    [Flips7.kicad_pcb, Flips7.sch]
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2018-11-14 Shifting board connector to get space for mounting pads
    [Flips7.kicad_pcb]
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2018-11-14 moving text, adding lines to visually group driver ics and corresponding connectors
    [Flips7.kicad_pcb]
2018-11-14 Adding Flips Logo
    [Flips7.kicad_pcb]
2018-11-14 single GND, VCC, HV for Flips5X
    [Flips5X.kicad_pcb, Flips5X.sch]
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2018-11-15 narrow tracing of Flips6c
    [Flips6c.kicad_pcb]
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2018-11-15 fixing missing VCC connection
    [Flips5X.kicad_pcb]
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2018-11-16 rename some symbols
    rename L.## and R.## nets to Y1.## and Y2.##
    rename CN1 and CN2 to SHR1 and SHR2
    rename U1/2/3 to IC1/2/3
    [Flips7.kicad_pcb, Flips7.sch]
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2018-11-16 renaming footprint references
    U1/2/3 to IC1/2/3
    swap R1 and R2
    [Flips6c.kicad_pcb, Flips6c.sch]
2018-11-16 Rename Flips6c description
    [Flips5X.kicad_pcb]
2018-11-16 Replace mounting holes: use variants with pad
    [Flips5X.kicad_pcb]
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2018-11-18 Changing pin names in mapping table on back side silk screen
    [Flips6.kicad_pcb]
2018-11-18 move pcb to (2 in | 2 in)
    [Flips6.kicad_pcb]
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2018-11-19 fix footprint of 74595 to SOIC-16_3.9x9.9mm_Pitch1.27mm
    [Flips6.kicad_pcb, Flips6.sch]
2018-11-19 Correcting some traces
    [Flips6.kicad_pcb]
2018-11-20 Adding Rows 21-28 (extra connector; preliminary pin assignment)
    [Flips5.kicad_pcb, Flips5.sch]
2018-11-20 adding "+20P" in silk screen and descriptions; adding 3d model for row driver; cleaning up traces
    [Flips5.kicad_pcb]
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2018-11-22 Fix icon footprint positions
    [Flips5.kicad_pcb]
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2018-11-25 Adding gerbers and aux files for Release V1.0 of Flips5/6/7
    [Flips5-B.Cu.gbr, Flips5-B.Mask.gbr, Flips5-B.SilkS.gbr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]
2018-11-25 fixing huge solder mask spacing
    [Flips5.kicad_pcb, Flips7.kicad_pcb]
2018-11-25 fixing flips logo
    [Flips5.kicad_pcb, Flips6.kicad_pcb, Flips7.kicad_pcb]
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2018-11-26 adding empty flips8
    [Flips8.kicad_pcb, Flips8.sch]
2018-11-26 starting Flips8 - NCV7708 based Annax Display Driver
    [Flips8.kicad_pcb, Flips8.sch]
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2018-11-28 proceed with Flips8
    [Flips8.kicad_pcb, Flips8.sch]
2018-11-29 finish initial routing of Flips8
    [Flips8.kicad_pcb]
2018-12-01 Place FP2800As' bypass capacitors and EN-pulldowns to fit in Dip40 socket
    [Flips5.kicad_pcb]
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2018-12-02 rearrange connector and decoder; move 'bus' away from board edge pt. 1
    [Flips8.kicad_pcb]
2018-12-02 fixing supply connection between ICs and capacitors
    [Flips8.kicad_pcb]
2018-12-02 adding bypass capacitor for decoder in flips
    [Flips8.kicad_pcb, Flips8.sch]
2018-12-10 Fix wrong labels of Flips6 uP connector: LAT <--> CLK
    [Flips6.kicad_pcb]
2018-12-13 Fix software folder structure to get using library work
    [Flips.ino]
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2018-12-21 fixing leftover trace
    [Flips6.kicad_pcb]
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2019-01-27 Adding draft of Flips15
    [Flips15.kicad_pcb, Flips15.sch, Group.sch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]
2019-01-27 rework Flips15 draft
    [Flips15.kicad_pcb, Group.sch, Unit.sch]
2019-01-27 Flips15 to only use 1 unit
    [Flips15.kicad_pcb, Flips15.sch, Group.sch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]
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2019-01-29 adding traces for flips 15
    [Flips15.kicad_pcb]
2019-01-31 more traces for flips15
    [Flips15.kicad_pcb]
2019-02-01 more tracing in flips15
    [Flips15.kicad_pcb]
2019-02-01 adding fill for flips15
    [Flips15.kicad_pcb]
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2019-02-02 tracing Flips15
    [Flips15.kicad_pcb]
2019-02-02 Adding more solder jumpers to overlapping pins of BRDIC1 and BROSE34
    [Flips15.kicad_pcb, Flips15.sch]
2019-02-02 more tracing Flips15
    [Flips15.kicad_pcb]
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2019-02-03 move driver ics to get more space for decoders and control connector
    [Flips15.kicad_pcb]
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2019-02-03 Adding control wires - removing control for channel 0 - placing capacitor
    [Flips15.kicad_pcb, Group.sch, Unit.sch]
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2019-02-04 moving pcb to get space for upper right mounting hole
    [Flips15.kicad_pcb]
2019-02-05 Finish remaining connection on Flips15
    [Flips15.kicad_pcb]
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2019-02-05 Fixing alignment of board to 0.025 in grid
    [Flips15.kicad_pcb]
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2019-02-06 more silk screen (use more compact IC values)
    [Flips15.kicad_pcb, Group.sch, Unit.sch]
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2019-02-06 adding support for optional COM pin at BRDIC1
    [Flips15.kicad_pcb, Flips15.sch, Group.sch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]
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2019-02-23 adding experimental Flips10 for replacing FP2800A
    [Flips10.kicad_pcb, Flips10.sch, Group.sch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]
2019-02-23 splitting Flips10 into driver and base
    [Flips10Base.kicad_pcb, Flips10Base.sch, Flips10Driver.kicad_pcb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]
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2019-02-23 using own component SR28GR as connector for Flips10
    [Flips10Base.sch, Flips10Driver.sch]
2019-02-24 progress for flips10 base
    [Flips10Base.kicad_pcb, Flips10Base.sch]
2019-03-01 adding Flips9
    [Flips9.kicad_pcb, Flips9.sch, Group.sch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]
2019-03-04 prepare traces of flips9
    [Flips9.kicad_pcb]
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2019-03-04 adding extra 16 pin connector instead of reusing 24-pin connector
    [Flips9.kicad_pcb, Flips9.sch]
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2019-03-06 finish flips9 routing
    [Flips9.kicad_pcb]
2019-03-07 fixing GND THT pad orientation
    [Flips9.kicad_pcb]
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
